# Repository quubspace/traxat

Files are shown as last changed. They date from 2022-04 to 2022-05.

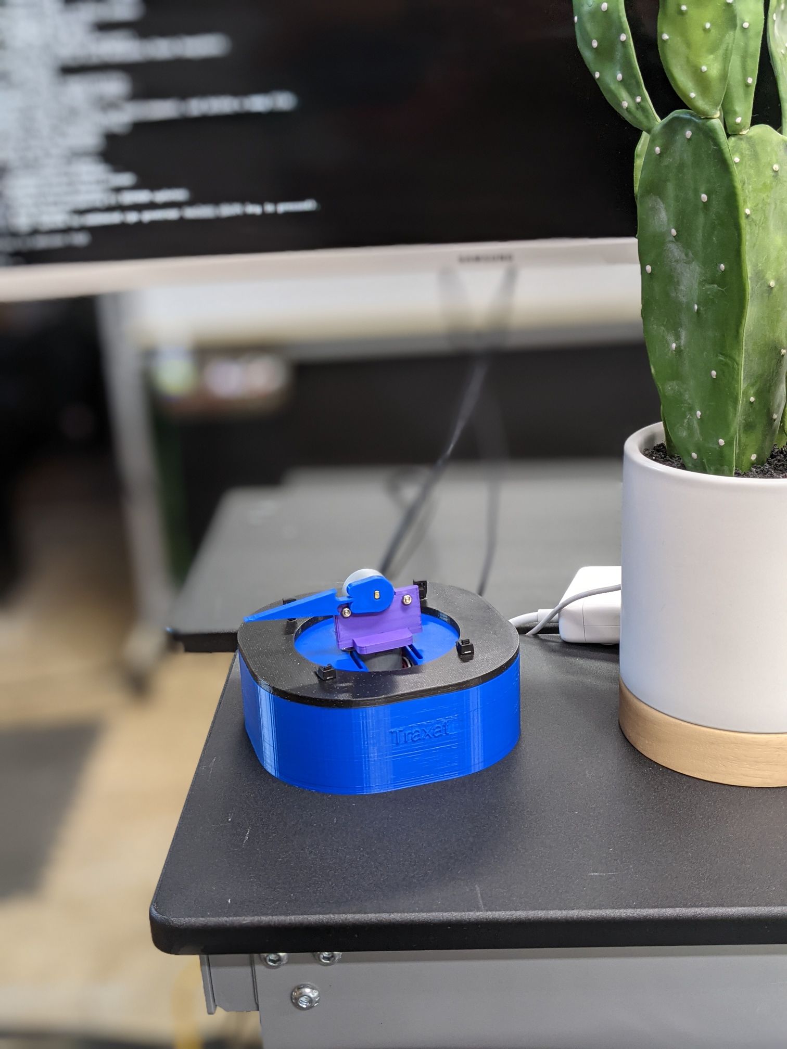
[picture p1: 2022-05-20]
images/assembled-unit.jpg

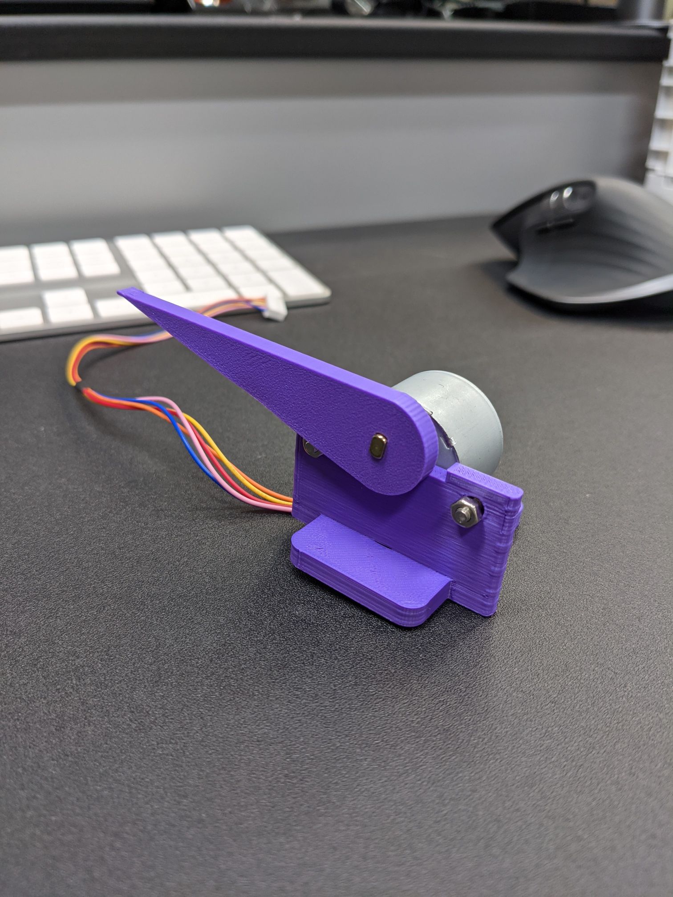
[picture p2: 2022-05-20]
images/platform-assembly.jpg

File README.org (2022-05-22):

#+BEGIN_HTML
<div id="traxat-logo" align="center">
    <br />
    <img src="images/logo.svg" alt="Traxat Logo" width="225" height="225"/>
    <h1>Traxat</h1>
    <h3>Open Source Tabletop Satellite Tracker</h3>
</div>

<div id="badges" align="center">

  <a href="https://github.com/quubspace/traxat/actions/workflows/software.yml">
    <img src="https://github.com/quubspace/traxat/actions/workflows/software.yml/badge.svg?branch=main" alt="GitHub Workflow Status"/>
  </a>

</div>
#+END_HTML
** About
The Traxat project is an open-source and open hardware tabletop satellite tracker.
This repository contains the Rust code for the firmware, the CAD models, and
instructions for constructing your own Traxat. Fully compatible with GPredict,
Traxat utilises hamlib and rotctld to enable wide compatibility with a wide
variety of programs.

We are constantly looking to improve the Traxat project, both in design and in
documentation. Feel free to open an issue or PR!

** Usage
The project only supports GPredict for tracking, although hypothetically you can
use a different program.

1. Open GPredict on a separate computer. Within GPredict's settings, you should
   see the ability to add radios and rotators. Add your Traxat unit's IP address
   as a rotator, and keep the default port.

2. Traxat does not automatically zero. In order to do so manually, push the
   pointer all the way to the left, and line up the motor as close to center as
   you can.

3. Power on your Traxat unit. If you followed the system service instructions
   when assembling, this is all you need to do.

4. Back in GPredict, you should see a small drop-down arrow near a map. When you select this, you will see rotator control. Click the menu.

5. You should now see a new window with various numbers. On the right side, you
   should see the name of your Traxat unit and an engage button. Once you select
   that, Traxat should start tracking.

6. For further problems, consider opening an issue.

** Building
*** Software
Traxat is guaranteed to build on the Raspberry Pi 4B+ and on the Raspberry Pi
3B+. It appears to build correctly on the M1 MacBook Pro as well, but all other
platforms aren't directly supported.

Traxat is written in Rust, so you will need to have a Rust installation in order to
compile it. Traxat is guaranteed to compile with Rust 1.59.0 (stable) or newer, but
older versions may also work.

To build Traxat:

#+BEGIN_SRC shell
$ git clone https://github.com/quubspace/traxat
$ cd traxat/software # To move into the software directory
$ cargo build --release
#+END_SRC

Once finished, you can try running Traxat:

#+BEGIN_SRC shell
$ cd ../ # So we are in the root of the project
$ ./software/target/release/traxat
#+END_SRC

In order to use Traxat on system start, copy the service file and binary as root and enable the ~systemd~ service:

#+BEGIN_SRC shell
$ sudo cp ./software/target/release/traxat /usr/bin
$ sudo chmod a+x /usr/bin/traxat # So the program is executable
$ sudo cp traxat.service /etc/systemd/system/
$ sudo systemctl enable --now traxat
#+END_SRC

A static IP is recommended for the Raspberry Pi so that your tracking program
can consistently connect to the unit, and through testing ethernet is more
consistent than Wi-Fi.

*** Hardware
The Traxat unit consists of 3D-printed parts, screws, stepper motors, and a
Raspberry Pi unit (preferably a Pi 4B+ for optimal performance).

The STLs for the 3D-printed parts are included in ~/hardware~.

**** Bill of Materials
| Qty | Item                 | Notes                                                                 |
|-----+----------------------+-----------------------------------------------------------------------|
|   1 | Raspberry Pi 4B+ 1GB | Any Pi 4 can be swapped in                                            |
|   1 | Each 3D-Printed Part | Parts can be printed in PLA or preferred material                     |
|   2 | Stepper Motors       | Can use any stepper motor, but platform is designed for specified one |
|   8 | M3 Screws and Nuts   | Holds the unit together                                               |

**** Assembly
1. Place your Raspberry Pi in the base, with power ports facing towards the side
opening.

#+BEGIN_HTML
<p align="center">
  <img src="./images/raspberry-pi-in-base.jpeg" alt="A Raspberry Pi placed into the base of the unit" width="300"/>
</p>
#+END_HTML

2. Screw a stepper motor onto the carriage, using the slots to adjust
where you want your motor.

3. Attach the second stepper motor to the platform, pushing the connector
   through the bottom hole and using the screws to fasten it together.

#+BEGIN_HTML
<p align="center">
  <img src="./images/platform-assembly.jpg" alt="Platform assembly for Traxat unit" width="300"/>
</p>
#+END_HTML

4. Place the platform assembly on top of the first motor on the carriage, and
   route the connectors down to the Pi.

5. Connect the motor control boards to the motors, and then wire them to the
   Raspberry Pi as shown in the first photo and documented in
   ~software/src/rotator.rs~. Ensure your azimuth and elevation are not flipped.

6. Use the remaining screws to screw the carriage to the lid.

7. Marvel at your finished Traxat unit!

#+BEGIN_HTML
<p align="center">
  <img src="./images/assembled-unit.jpg" alt="Finished Traxat unit" width="300"/>
</p>
#+END_HTML

** Testing

To run manual step tests, make use of the included ~manual_testing.sh~ found in
~/software~. Simply run ~./manual_testing.sh 10~, where 10 is the number of
motor steps to run.

** Credits
Initial prototypes of Traxat were inspired by PiTator by @M0JEC on GitHub. Thank
you to everyone at Quub for your continued support as well.

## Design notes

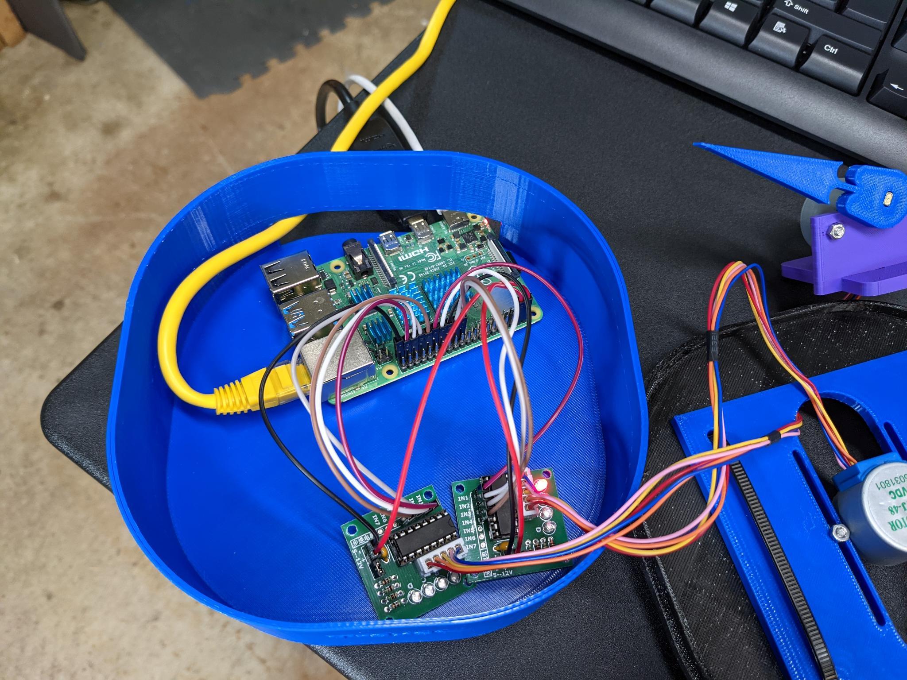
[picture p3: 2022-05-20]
images/raspberry-pi-in-base.jpeg

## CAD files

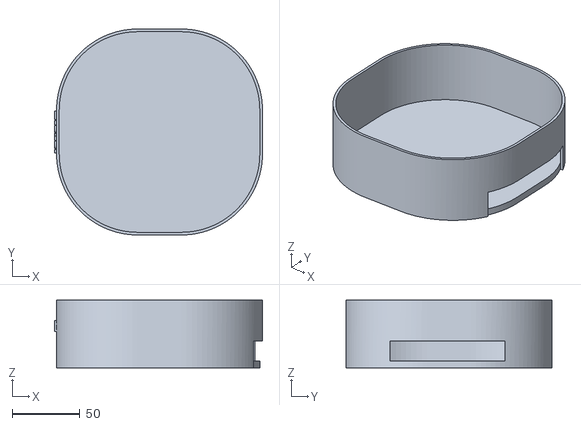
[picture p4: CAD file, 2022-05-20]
hardware/Base.stl
153.9 x 152.4 x 50.0

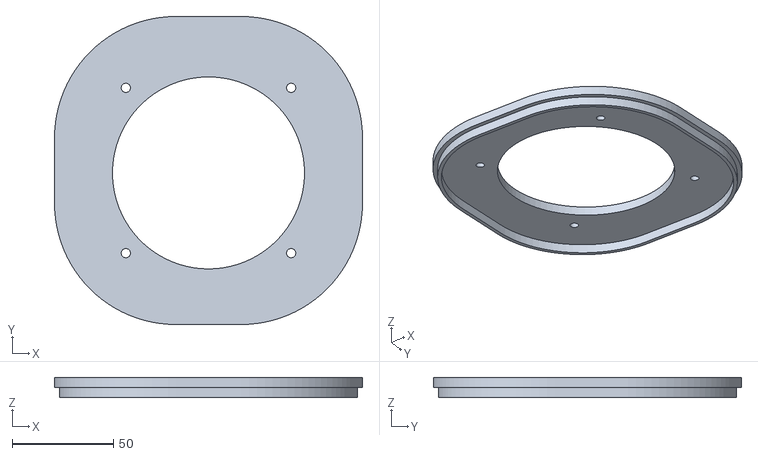
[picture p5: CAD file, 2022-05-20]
hardware/Lid.stl
152.4 x 152.4 x 10.0

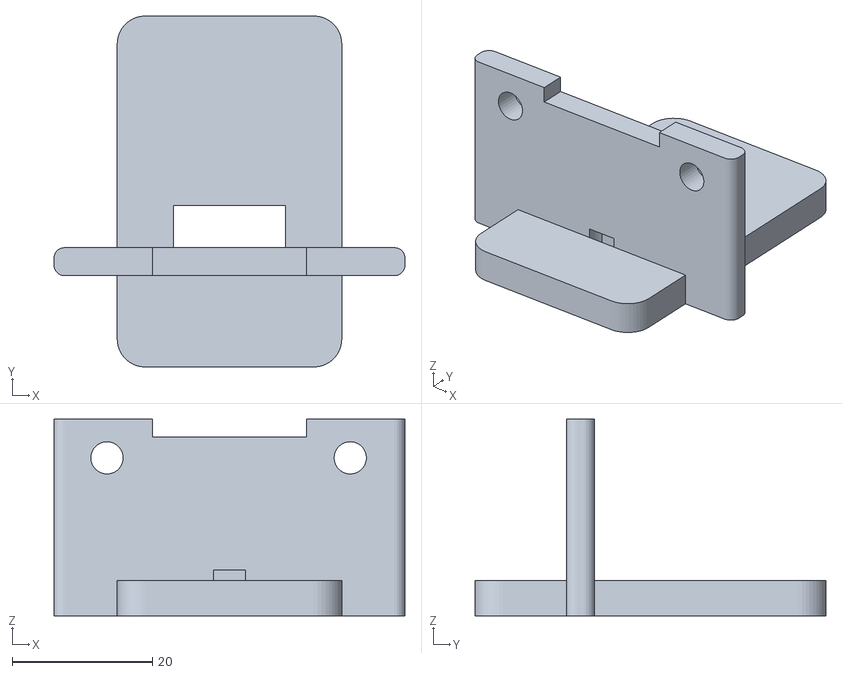
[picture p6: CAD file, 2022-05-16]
hardware/Platform.stl
50.0 x 50.0 x 28.0

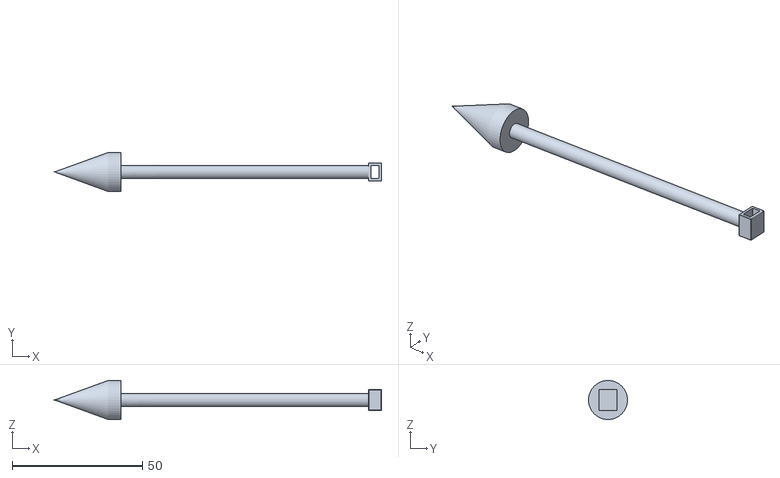
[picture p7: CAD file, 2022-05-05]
hardware/Pointer.stl
125.6 x 15.0 x 15.0

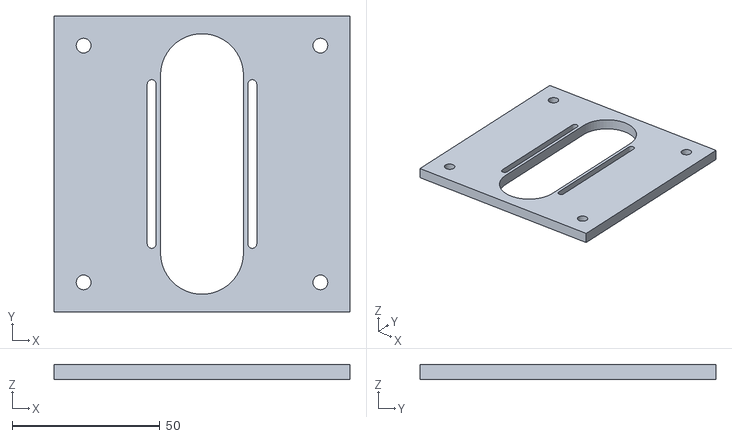
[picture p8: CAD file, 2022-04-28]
hardware/Carriage.stl
100.0 x 100.0 x 5.00

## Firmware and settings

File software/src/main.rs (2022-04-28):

use std::{
    io::{self, Read, Write},
    net::TcpListener,
    str::{self, FromStr},
};

use anyhow::Result;

use fern::{
    colors::{Color, ColoredLevelConfig},
    log_file, Dispatch,
};
use log::{debug, info, warn, LevelFilter};

// Imports items from other crates
use handler::ActionHandler;
use message::Message;
use rotator::Rotator;

// Organizes code into modules
mod handler;
mod message;
mod rotator;

/// Main function to run the traxat software
fn main() -> Result<()> {
    // Initializes logging with Criterion
    init_logging();

    // Create a new rotator object.
    let mut rotator = Rotator::new();

    // Sets the motor position to zero.
    rotator.zero()?;

    // Opens a TCP listener on port 4533
    let rotctld_port = "4533";
    let listener = TcpListener::bind(format!("0.0.0.0:{}", rotctld_port))?;

    info!("AST is now ready to connect to rotctld.");

    // Listen for rotctld commands and execute them coming in.
    for stream in listener.incoming() {
        let mut stream = stream?;
        let mut buf = [0; 1024];

        // Read data coming in.
        loop {
            let n = match stream.read(&mut buf) {
                Ok(n) if n == 0 => break,
                Ok(n) => n,
                Err(e) => {
                    warn!("Failed to read from stream; err = {:?}", e);
                    break;
                }
            };

            let response = str::from_utf8(&buf[0..n]).unwrap();
            debug!("Response from rotctld: {:?}", response);

            // This will never actually error, since it returns Infallible
            let ret: String = ActionHandler::new(&mut rotator)
                .handle_message(Message::from_str(response).unwrap())?;

            // Quit command to close connection.
            if ret == "rotctld_quit" {
                warn!("Closing connection, rotctld sent quit!");
                rotator.zero()?;
                break;
            }

            // Sending
            debug!("Send to rotctld: {:?}", ret);

            if let Err(e) = stream.write_all(&buf[0..n]) {
                warn!("failed to write to stream; err = {:?}", e);
                break;
            }
        }
    }
    Ok(())
}
/// Initializes logging.
///
/// Changes the colors and format of the logging.
fn init_logging() {
    let colors_line = ColoredLevelConfig::new()
        .error(Color::Red)
        .warn(Color::Yellow)
        .info(Color::White)
        .debug(Color::White)
        .trace(Color::BrightBlack);

    let colors_level = colors_line.info(Color::Green);

    Dispatch::new()
        .format(move |out, message, record| {
            out.finish(format_args!(
                "{color_line}[{date}][{target}][{level}{color_line}] {message}\x1B[0m",
                color_line = format_args!(
                    "\x1B[{}m",
                    colors_line.get_color(&record.level()).to_fg_str()
                ),
                date = chrono::Local::now().format("%Y-%m-%d %H:%M:%S"),
                target = record.target(),
                level = colors_level.color(record.level()),
                message = message,
            ));
        })
        .level(LevelFilter::Debug)
        .level_for("pretty_colored", LevelFilter::Trace)
        .chain(io::stdout())
        .chain(log_file("./ast.log").expect("No permission to write to the current directory."))
        .apply()
        .expect("Failed to dispatch Fern logger!");

    debug!("Logging initialization complete.");
}

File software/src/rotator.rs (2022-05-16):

use rppal::{gpio::Gpio, system::DeviceInfo};

use anyhow::Result;

use std::{thread, time::Duration};

use log::info;

// Pin map
// 6 => ELE1 A
// 13 => ELE2 B
// 19 => ELE3 A_
// 26 => ELE4 B_

// 9 => AZ1 A
// 11 => AZ2 B
// 0 => AZ3 A_
// 5 => AZ4 B_

const MOTOR_ELE_GPIO: [u8; 4] = [6, 13, 19, 26];
const MOTOR_AZ_GPIO: [u8; 4] = [9, 11, 0, 5];
const STEPS_PER_ROT: f32 = 512.0;

#[derive(Debug)]
/// Rotator struct for traxat
pub struct Rotator {
    /// Elevation
    pub ele: f32,
    /// Azimuth
    pub az: f32,
    /// Y axis target position
    pub ele_target: f32,
    /// X axis target position
    pub az_target: f32,
    /// Number of steps to go
    pub num_steps: i32,
}

impl Rotator {
    /// Returns a rotator instance from a string
    ///
    /// # Arguments
    ///
    /// * `response` - A message in the form of a string
    ///
    pub fn new() -> Rotator {
        Rotator {
            // Based on the implemented logic, this will auto-zero when disengaged and first booted up
            ele: 0_f32,
            az: 0_f32,
            ele_target: 0_f32,
            az_target: 0_f32,
            num_steps: 0_i32,
        }
    }

    /// Returns the Result of moving a certain amount of steps
    pub fn mv(&mut self) -> Result<()> {
        let steps_per_degree = (STEPS_PER_ROT / 360.0) as f32;
        let ele_steps = (self.ele_target - self.ele) * steps_per_degree as f32;
        let az_steps = (self.az_target - self.az) * steps_per_degree as f32;
        info!("ele_steps is {}.", ele_steps);
        info!("az_steps is {}.", az_steps);
        info!("steps_per_degree is {}.", steps_per_degree);

        // Move elevation stepper
        if ele_steps != 0.0 {
            self.move_steppers(ele_steps, &MOTOR_ELE_GPIO)?;
        }

        // Move azimuth stepper
        if az_steps != 0.0 {
            self.move_steppers(az_steps, &MOTOR_AZ_GPIO)?;
        }

        self.ele = self.ele_target;
        self.az = self.az_target;

        info!("Elevation is {}, Azimuth is {}.", self.ele, self.az);

        Ok(())
    }

    /// Returns a Result of zeroing the traxat
    pub fn zero(&mut self) -> Result<()> {
        self.ele_target = 0_f32;
        self.az_target = 0_f32;

        self.mv()?;

        Ok(())
    }

    /// Returns a Result of testing the stepper
    pub fn test_steppers(&self) -> Result<()> {
        let cur_steps = self.num_steps;
        info!("Moving motor {} steps", cur_steps);
        self.test_move_steppers(cur_steps, &MOTOR_ELE_GPIO)?;

        Ok(())
    }

    /// Returns the result of testing the move of the steppers
    ///
    /// # Arguments
    ///
    /// * `steps` - Amount to move
    ///
    /// * `gpio_pin_list` - Reference to the list of gpios
    ///
    fn test_move_steppers(&self, steps: i32, gpio_pin_list: &[u8]) -> Result<()> {
        let abs_steps = steps.abs();
        info!("Moving motor on a {}.", DeviceInfo::new()?.model());

        for _ in 0..abs_steps {
            if steps >= 0 {
                self.step_pins_forward(gpio_pin_list)?;
            } else {
                self.step_pins_backward(gpio_pin_list)?;
            }
        }

        info!("Done!");

        Ok(())
    }

    /// Returns the result of moving the steppers
    ///
    /// # Arguments
    ///
    /// * `steps` - Amount to move
    ///
    /// * `gpio_pin_list` - Reference to the list of gpios
    ///
    fn move_steppers(&self, steps: f32, gpio_pin_list: &[u8]) -> Result<()> {
        info!("Moving motor on a {}.", DeviceInfo::new()?.model());
        let abs_steps = steps.abs().floor() as i32;

        for _ in 0..abs_steps {
            if steps >= 0.0 {
                self.step_pins_forward(gpio_pin_list)?;
            } else {
                self.step_pins_backward(gpio_pin_list)?;
            }
        }

        info!("Done!");

        Ok(())
    }

    /// Returns the result of stepping the pins forward
    ///
    /// # Arguments
    ///
    /// * `pins_list` - Reference to the list of pins
    ///
    fn step_pins_forward(&self, pins_list: &[u8]) -> Result<()> {
        let delay_set = 2;

        let mut a1 = Gpio::new()?.get(pins_list[0])?.into_output();
        let mut b1 = Gpio::new()?.get(pins_list[1])?.into_output();
        let mut a2 = Gpio::new()?.get(pins_list[2])?.into_output();
        let mut b2 = Gpio::new()?.get(pins_list[3])?.into_output();

        // Full-step sequence
        // Quarter-step 1
        a1.set_high();
        b1.set_low();
        a2.set_low();
        b2.set_high();
        thread::sleep(Duration::from_millis(delay_set));

        // Quarter-step 2
        a1.set_high();
        b1.set_high();
        a2.set_low();
        b2.set_low();
        thread::sleep(Duration::from_millis(delay_set));

        // Quarter-step 3
        a1.set_low();
        b1.set_high();
        a2.set_high();
        b2.set_low();
        thread::sleep(Duration::from_millis(delay_set));

        // Quarter-step 4
        a1.set_low();
        b1.set_low();
        a2.set_high();
        b2.set_high();
        thread::sleep(Duration::from_millis(delay_set));

        // Motor off
        a1.set_low();
        b1.set_low();
        a2.set_low();
        b2.set_low();

        Ok(())
    }

    /// Returns the result of setting pins back
    ///
    /// # Arguments
    ///
    /// * `pin_list` - Reference to a list of pins
    ///
    fn step_pins_backward(&self, pins_list: &[u8]) -> Result<()> {
        let delay_set = 2;

        let mut a1 = Gpio::new()?.get(pins_list[0])?.into_output();
        let mut b1 = Gpio::new()?.get(pins_list[1])?.into_output();
        let mut a2 = Gpio::new()?.get(pins_list[2])?.into_output();
        let mut b2 = Gpio::new()?.get(pins_list[3])?.into_output();

        // Full-step sequence

        // Step 4
        a1.set_low();
        b1.set_low();
        a2.set_high();
        b2.set_high();
        thread::sleep(Duration::from_millis(delay_set));

        // Step 3
        a1.set_low();
        b1.set_high();
        a2.set_high();
        b2.set_low();
        thread::sleep(Duration::from_millis(delay_set));

        // Step 2
        a1.set_high();
        b1.set_high();
        a2.set_low();
        b2.set_low();
        thread::sleep(Duration::from_millis(delay_set));

        // Step 1
        a1.set_high();
        b1.set_low();
        a2.set_low();
        b2.set_high();
        thread::sleep(Duration::from_millis(delay_set));

        // Motor off
        a1.set_low();
        b1.set_low();
        a2.set_low();
        b2.set_low();

        Ok(())
    }
}

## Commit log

2022-02-26 Fix command responses and clean up logging
    [main.rs]
2022-02-27 Add basic logic for motors and update readme
2022-03-03 Fix deployment and add demo motor function
    [rotator.rs]
2022-03-10 Fix motor stepping
2022-03-10 Fix mutability of steps
    [rotator.rs]
2022-03-16 Fix bug where ele and az weren't updating
    [rotator.rs]
2022-03-16 Update delay time for steppers
2022-03-17 Testing stepper motors for accuracy
2022-03-24 Fix comments and naming conventions
    [rotator.rs]
2022-04-07 Changed one thing to get the contribution I didn't get from the last pull request.
    [main.rs]
2022-04-15 Separate hardware and software
    [Base.stl, Carriage.stl, Lid.stl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]
2022-04-21 Update carriage
    [Carriage.stl]
2022-04-28 Fixes documentation spelling and word choice
    [main.rs, rotator.rs]
2022-05-03 Update base with port holes and platform
    [Base.stl, Platform.stl]
2022-05-05 Add pointer model and update platform
    [Platform-v4.stl, Pointer.stl]
2022-05-05 Remove extra platform model
    [Platform-v4.stl, Platform.stl]
2022-05-11 Update platform
    [Platform.stl]
2022-05-20 Add updated base and lid
    [Base.stl, Lid.stl]
